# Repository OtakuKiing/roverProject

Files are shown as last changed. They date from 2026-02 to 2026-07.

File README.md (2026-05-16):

[//]: # (This is a comment format of Markdown files!)





# Project Overview

## What it is
Project Wayfinder is planned to be a relatively large (exact size TBD) autonomous rover vehicle, designed for 3D mapping and autonomous navigation via SLAM and computer vision algorithms. Designed from the ground up, the aim is to do much as possible via ground up implementation from first principles, while learning essential frameworks such as ROS2. 

The target design architecture: RasPi 4 (ROS2, autonomous nav and mapping), ESP32 (web interface and comms relay), Teensy 4.1 (microROS, real-time control)

## File Index

**[Arduino](/arduino)**  
    ├> [Local libraries](/arduino/lib)  
    ├> [Source Code](/arduino/src)  
    └> [Header files](/arduino/include)  

**[Ground Controller](/ground-controller)**  
		├> [ROS2](/ground-controller/ros2-workspace)
    └> [Python](/ground-controller/python) (via PyGame & PySerial)

**[Docs](/_docs)**  
    ├> [Assets](/_docs/assets)  
    ├> [Subversion Info](/_docs/versioning) (complete breakdowns of each subversion)  
    ├> [Electronics](/_docs/electronics)  
    └> [Hardware](/_docs/hardware)  

## Getting Started  
Check out [contributions](/CONTRIBUTING.md) before editing anything!

Wayfinder is built mainly on *Linux* infrastructure (specifically Ubuntu 22.04); alternatives will be mentioned where possible.  

- Clone this repo and install the PlatformIO extension in your IDE
- Follow the [ROS2 "Humble" install guide](https://docs.ros.org/en/humble/Installation/Ubuntu-Install-Debs.html)

## Status
**Focus**: Arduino + ROS2 fundamentals, test rig development  

 - [X] Set up dev environment (ROS2 Humble, PlatformIO, Git)
 - [X] Finalize parts list for first purchase
 - [X] Serial communication, PWM motor control, encoder reading
 - [ ] ROS2 practice: Publisher/subscriber nodes, serial communication
 - [X] Design V0 test rig in Onshape

## Team & Credits
Project Lead - Michael Yakubu  
Hardware Design - Faisal Ibrahim, Yahia Eltahir  
Software Engineering - TBD  
Electronics Design - TBD  

### License
See [LICENSE](/LICENSE) for more details.

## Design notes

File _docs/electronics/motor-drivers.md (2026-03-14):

# Motor Driver Boards

Driver boards which allow the motor to recieve commands from the real-time microcontroller. Though motors can theoretically be directly connected to the microcontroller, the 5V output and low current wouldn't be enough for anything beyond the smallest of hobby motors. There's also a risk of damaging the GPIO pins due to back EMF (motor sending high voltage back to power supply).

### In the specs...

Current is written as `[max continuous draw]/[peak draw]`.  
Safety margin is calculated as `[max continouos draw]/[peak motor draw]`.

## V0
### Options and Specs
**Model A**: [Dual channel 10A](https://thepihut.com/products/10a-5v-30v-2-channel-dc-motor-driver)  
**Specs**:  
 - Channels: 2  
 - Current: 10/30A  
 - Voltage: 5/30V  
 - Reverse Polarity Protection (RPP): No  
 - I/O Pins: 4  
 - Cost: £22.20  

**Model B**: [Dual channel 7A](https://thepihut.com/products/2x7a-dc-motor-driver)  
**Specs**:  
 - Channels: 2  
 - Current: 7/50A  
 - Voltage: 7/24V  
 - Reverse Polarity Protection (RPP): Yes  
 - I/O Pins: 6  
 - Cost: £20.20  

**Model C**: [Single channel 43A](https://www.amazon.co.uk/JZK-BTS7960B-Double-Stepper-H-Bridge/dp/B09HGBM5D2)  
**Specs**:  
 - Channels: 1  
 - Current: 43A (likely cont.)  
 - Voltage: 5.5/27V  
 - Reverse Polarity Protection (RPP): N/A  
 - I/O Pins: 6 
 - Cost: £7.19  

### Key Notes and Comparisons
- Model C is a single channel board and thus is the cheapest option; one board per motor means greater redundancy, but takes up more space.  
- Model C also seems to have the highest continuous current output per channel (unconfirmed), more than 6x that of Model B. However, the V0 motors draw a max of 7A each, so only Model A lacks a safety margin.  
- Model A lacks RPP, but this can be mitigated via thorough wiring checks.  

### Final Decision
**Model A** is the best V0 choice - it has the most appropriate safety margin, and requires the fewest I/O pins for full control. The lack of RPP does pose risk, but this is offset by its clear labelling and addition of test buttons. Model B can also easily be used as an alternative, though not at full motor load.

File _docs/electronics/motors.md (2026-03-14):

# Motors

High quality motors are an essential component for any mobile vehicle project, and so selecting the appropriate models is key.
  
## In the specs...
Encoder values are written as `[motor shaft count]/[output shaft count]` CPR (Counts Per Revolution). For example, a `24/72` CPR encoder reads at 24 CPR on the motor shaft and 72 CPR on the output shaft, describing a 1:3 geared motor.  
Current values are written as `[min. current]/[stall current]` A. For example, a `0.35/6` A motor runs at 0.35A under no load ad has a maximum draw of 6A.

## V0
### Options and Specs
**Model A**: [12V 251RPM 18kgcm](https://thepihut.com/products/metal-dc-geared-motor-w-encoder-12v-251rpm-18kg-cm)  
**Specs**:  
 - Output Shaft: 6mm D-shaft
 - Torque: 18kgcm  
 - Speed: 251 RPM  
 - Encoder: 16/700 CPR, Hall sensor
 - Voltage: 12V  
 - Current: 0.35/7A  
 - Weight: 205g
 - Cost: £15.90  

**Model B**: [12V 122RPM 38kgcm](https://thepihut.com/products/metal-dc-geared-motor-w-encoder-12v-122rpm-38kg-cm)  
**Specs**:  
 - Output Shaft: 6mm D-shaft
 - Torque: 38kgcm  
 - Speed: 122 RPM  
 - Encoder: 16/1440 CPR, Hall sensor
 - Voltage: 12V  
 - Current: 0.35/7A  
 - Weight: 205g
 - Cots: £27.90    

### Key Notes & Comparisons
Model B has more than 2x more torque than Model A, but this is unimportant as both can handle the full weight of V0.  
Using 80mm wheels at half of max RPM, Model A and B could achieve `pi*0.08*125.5/60 = 0.53 m/s` and `pi*0.08*61/60 = 0.26 m/s` respectively due to RPM differences.  
B has double the effective encoder precision, but this is unimportant as precise wheel precision is unnecessary here.
B is also twice as expensive due to the higher internal gear ratio.

### Final Decision
**Model A** is the best V0 choice - much lower cost while providing a suitably modest amount of torque and encoder accuracy compared to alternatives. It has (at best) double the velocity and still matches power system requirements perfectly. The 6mm D-shaft is also a common size and suits many COTS wheels via direct drive.

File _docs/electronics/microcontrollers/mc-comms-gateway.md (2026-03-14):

# Communication Gateway
Wireless communication is a must for any autonomous vehicle, allowing live data streams to be viewed and remote control overrides. This task could be given to a dedicated microcontroller for better micromanagement, or added onto an existing MCU for lower latency/complexity and fewer failure points.  

### In the specs...
Describe how specs are laid out + other info that may help understand the page

## V0
### Options and Specs  
**Model A**: [ESP32-S3](Link)  
**Specs**:  
 - Supported protocols: 
 - Wireless transfer rate:  
 - Max range:  
 - Frequency:  
 - GPIO: 13
 - Cost:

**Model B**: [Item](Link)  
**Specs**:  
 - Supported protocols:
 - Wireless transfer rate:  
 - Max range:  
 - Frequency:  
 - GPIO:
 - Cost:

### Key Notes & Comparisons

### Final Decision

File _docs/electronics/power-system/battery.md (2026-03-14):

# Battery  
Short description describing component and its importance  

### In the specs...  
Discharge rate is written as `[Max continuous current]/[Peak current]`.  

## V0  
### Options and Specs
**Model A**: [3S 2200mAh LiPo battery](https://overlander.co.uk/product/2200mah-11-1v-3s-35c-supersport-pro-lipo-battery/)  
**Specs**:  
 - Capacity: 2200mAh
 - Discharge rate: 77/143A
 - Voltage: 11.1V
 - Weight: 169g
 - Cost: £17.99

**Model B**: []()  
**Specs**:  
 - Capacity: 
 - Discharge rate: 
 - Voltage: 
 - Weight: 
 - Cost:

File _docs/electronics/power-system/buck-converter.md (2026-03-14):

# Buck Converter
Different components often operate at different voltages, but a battery can only provide one voltage level. You could use several batteries to group a system into its various voltages, but a much simpler solution is to convert, for example, 12V into 5V using a buck converter.

### In the specs...
Describe how specs are laid out + other info that may help understand the page

## V0
### Options and Specs  
**Model A**: [5V 1.2A MPM3610](https://thepihut.com/products/adafruit-mpm3610-5v-buck-converter-breakout-21v-in-5v-out-at-1-2a)  
**Specs**:  
 - V-in: 6/21V
 - V-out: 5V
 - Max current: 1.2A
 - Pre-soldered: No
 - Cost: £6.00

**Model B**: [20W Adjustable Converter](https://thepihut.com/products/20w-adjustable-dc-dc-buck-converter-with-digital-display)  
**Specs**:  
 - V-in: 4/40V
 - V-out: 3V3/5V
 - Max current: 5/3A
 - Pre-soldered: Yes
 - Cost: £4.70 

### Key Notes & Comparisons
Model A only outputs a fixed voltage and current, whereas B can provide a wide range (6W vs 20W respectively).
A is potentially much cooler than B at the same voltage due to its lower max current.
A has a significantly smaller footprint than B, but lacks conveniences such as self-calibration and RPP.

### Final Decision
**Model B** is the best choice for V0, as it has a much larger safety margin in terms of current, can output over twice as much power, and comes with pre-soldered connectors. The adjustable voltage also means it can be re-used for other components. Model A may be good for future use in isolated circuits where space and simplicity are essential.

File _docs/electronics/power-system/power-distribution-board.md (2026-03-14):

# Power Distribution Board
Short description describing component and its importance
  
### In the specs...
Describe how specs are laid out + other info that may help understand the page

## V0
### Options and Specs  
**Model A**: [Item](Link)  
**Specs**:  
 - Max V-out:
 - Max current:
 - Channels:
 - Connectors:
 - Cost:

**Model B**: [Item](Link)  
**Specs**:  
 - Max V-out:
 - Max current:
 - Channels:
 - Connectors:
 - Cost:   

### Key Notes & Comparisons

### Final Decision

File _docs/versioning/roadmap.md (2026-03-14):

# Roadmap
> A quick index of each version, including subversions.

| Version | Name | Status | Summary |
|---|---|---|---|
| v0.0 | Keyframe | Active | 2WD test rig, closed-loop PID |
| v0.1 | Crawler | Planned | ROS2 nodes, PlotJuggler |
| v1.0 | TBD | Planned | 4WD platform, sonar |
| v2.0 | TBD | Planned | RasPi, first SLAM attempt |
| vF | Wayfinder | Target | Full LiDAR/vision UGV |

## Progression Summary

```text
V0:
    Hardware:	      2WD, Differential steering, 3DP/Lasercut chassis
    Sensors:	      Wheel encoders, Buzzer, IMU
    Controllers:	  Arduino (C++)

V1:
    Hardware:	      4WD, Differential steering, COTS/Lasercut chassis
    Sensors:	      Wheel encoders, Buzzer, Sonar, LED screen
    Controllers:	  Arduino (C++), ESP32-S3

V2:
    Hardware:	      4WD, Differential steering, Aluminum chassis
    Sensors:	      Wheel encoders, Buzzer, Sonar, LED screen, Environmental sensor suite
    Controllers:	  Arduino (C++), ESP32-S3, RasPi 4B

...	etc

VF:
    Application:    Area mapping, surveillance, data collection, payload delivery, endurance missions,
    Hardware:       Aluminum chassis, AWD, AWS(?), Independent suspension 
    Sensors:        Odometry, LoRa telemetry, RTK GPS, LiDAR SLAM, Vision, Speakers, Lights
    Controllers:    Teensy 4.1 <-> ESP32 <-> RasPi, (micro)ROS2
    Modules:        [Stretch goals!] Robotic arm, Drone launcher, Solar 
```

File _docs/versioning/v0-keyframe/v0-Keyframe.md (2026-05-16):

# v0 "Keyframe"

> First stable closed-loop control on the 2WD test rig.

## Hardware
- **Chassis:** Lasercut wood plates
- **Motion:** 2WD differential
- **Controllers:** Arduino UNO R3
- **Sensors:** Wheel encoders, IMU (MPU6050)

## Firmware
- PID velocity controller
- Pygame serial bridge node
- Basic telemetry publisher

## Changelog

<details>
<summary><h2 style="display:inline">v0.0 "VERSION"</h2></summary>

### Added
- New stuff

### Fixed
- N/A

### Known Issues / Limitations
- Stuff that needs to be fixed

### Up Next
- What this lets us do next

</details><br>

<details>
<summary><h2 style="display:inline">v0.1 "Keyframe"</h2></summary>

### Added
- New stuff

### Fixed
- Fixed stuff

### Known Issues / Limitations
- Stuff that needs to be fixed

### Up Next
- What this lets us do next

</details>

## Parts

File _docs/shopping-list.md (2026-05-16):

# Shopping List

Parts listed in order of importance. `---` notates sets that should be **bought together** for each subversion.
Most parts come from the Pi Hut, but some may be sourced from sites such as Pimoroni or elsewhere.

| Component | Quantity | Cost £ |
| --- | --- | --- |
| **V0** | | |
| ~~[Arduino UNO R3](https://thepihut.com/products/arduino-uno-rev-3)~~																				 | 1 | 24.50  |
| ~~[12V motor w/ encoder](https://thepihut.com/products/metal-dc-geared-motor-w-encoder-12v-251rpm-18kg-cm)~~ | 2 | 31.80  |
| ~~[Half-size breadboard](https://thepihut.com/products/raspberry-pi-breadboard-half-size)~~									 | 1 | 3.00 |
| ~~[DuPont Wires](https://thepihut.com/products/thepihuts-jumper-bumper-pack-120pcs-dupont-wire)~~ | 1 | 6.00 |
| ~~[Piezo Buzzer](https://thepihut.com/products/piezo-buzzer)~~ | 1 | 1.30 |
| ~~[Electrolytic Capacitors](https://thepihut.com/products/200-piece-ultimate-capacitor-kit)~~ | 1 | 6.00 |
| ~~[Motor driver board](https://thepihut.com/products/10a-5v-30v-2-channel-dc-motor-driver)~~ | 1 | 22.20  |
| ~~[DC Jack to Screw Terminal]()~~ | 1 | 5.99 |
| ------------------------------------------- | -------- | 100.70 |
| ------------------------------------------- | -------- | ------ |
| [IMU](https://thepihut.com/products/adafruit-mpu-6050-6-dof-accel-and-gyro-sensor-stemma-qt-qwiic) | 1 | 8.00 |
| [Voltage/Current Sensor](https://thepihut.com/products/adafruit-ina260-high-or-low-side-voltage-current-power-sensor-ada4226)  | 1 | 9.60  | | -------- | ------ |
| [Buck converter](https://thepihut.com/products/dc-dc-buck-mini-module-3-3v-5v) | 2 | 6.80 |
| [Raspberry Pi Heatsink w/ Fan](https://thepihut.com/products/dual-fan-heatsink-case-for-raspberry-pi-4) | 1 | 14.00  |
| [Hubs](https://thepihut.com/products/pololu-universal-aluminium-mounting-hub-for-6mm-shafts-m3-holes-2-pack) | 1 | 12.50  |
| [80mm Wheels](https://thepihut.com/products/pololu-wheel-80x10mm-pair-black) | 1 | 8.40 |
| [3S 2200mAh LiPo battery](https://overlander.co.uk/product/2200mah-11-1v-3s-35c-supersport-pro-lipo-battery/)| 1 | 17.99  |
| [LiPo charger](https://overlander.co.uk/product/overlander-rc-3s-lipo-charger/) | 1 | 16.99  |
| [LiPo safety charge sack](https://overlander.co.uk/product/lipo-safety-charge-sack) | 1 | 7.99 |
| Shipping | -------- | 7.50 |
| **Subtotal** | -------- | 109.77 |
| | | |
| **V1** | | |
| [ESP32-S3](https://thepihut.com/products/adafruit-esp32-s3-feather-with-4mb-flash-2mb-psram-stemma-qt-qwiic) | 1 | 16.80  |
| [Teensy 4.1](https://thepihut.com/products/teensy-4-1-with-assembled-pins) | 1 | 34.60  |
| Aluminum extrusion | xxx | xxx |
| ------------------------------------------- | -------- | ------ |
| [BNO055 IMU](https://thepihut.com/products/adafruit-9-dof-absolute-orientation-imu-fusion-breakout-bno055) | 1 | 33.60  |
| [NEO-6M GPS](https://thepihut.com/products/adafruit-ultimate-gps-breakout-66-channel-w-10-hz-updates) | 1 | 28.80  |
| **Subtotal** | -------- | 113.80 |
| | | |
| **V2** | | |
| [RasPi 4B](https://thepihut.com/products/raspberry-pi-4-model-b) | 1 | 81.60  |
| [Ethernet for Teensy 4.1](https://thepihut.com/products/ethernet-kit-for-teensy-4-1) | 1 | 9.60 |
| ------------------------------------------- | -------- | ------ |
| [RPLIDAR](https://www.mouser.co.uk/ProductDetail/DFRobot/DFR0315?qs=kE1vTINknaX%252Bruj42CnW2Q%3D%3D) | 1 | 89.20  |
| [C270 camera](https://www.argos.co.uk/product/4034924) | 1 | 17.99  |
| **Subtotal** | -------- | 198.39 |
| | | |
| **Total** | | 493.26 |

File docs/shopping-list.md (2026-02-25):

# Shopping List

Parts listed in order of importance. `---` notates sets that should be **bought together** for each subversion.
Most parts come from the Pi Hut, but some may be sourced from sites such as Pimoroni or elsewhere.

| Component | Quantity | Cost £ |
| --- | --- | --- |
| **V0** | | |
| [Arduino UNO R3](https://thepihut.com/products/arduino-uno-rev-3)																						 | 1 | 24.50  |
| [12V motor w/ encoder](https://thepihut.com/products/metal-dc-geared-motor-w-encoder-12v-251rpm-18kg-cm) | 2 | 31.80  |
| [Half-size breadboard](https://thepihut.com/products/raspberry-pi-breadboard-half-size)											 | 1 | 3.00 |
| [DuPont Wires](https://thepihut.com/products/thepihuts-jumper-bumper-pack-120pcs-dupont-wire) 		 | 1 | 6.00 |
| [Piezo Buzzer](https://thepihut.com/products/piezo-buzzer) | 1 | 1.30 |
| [Electrolytic Capacitors](https://thepihut.com/products/200-piece-ultimate-capacitor-kit) | 1 | 6.00 |
| [Motor driver board](https://thepihut.com/products/10a-5v-30v-2-channel-dc-motor-driver) | 1 | 22.20  |
| [DuPont Wires](https://thepihut.com/products/thepihuts-jumper-bumper-pack-120pcs-dupont-wire) | 1 | 6.00 |
| [IMU](https://thepihut.com/products/adafruit-mpu-6050-6-dof-accel-and-gyro-sensor-stemma-qt-qwiic) | 1 | 8.00 |
| ------------------------------------------- | -------- | ------ |
| Assembly hardware | 1 | 30.00  |
| 6mm Birch Plywood | 1 | 20.00  |
| [Hubs](https://thepihut.com/products/pololu-universal-aluminium-mounting-hub-for-6mm-shafts-m3-holes-2-pack) | 1 | 12.50  |
| [Wheels](https://thepihut.com/products/pololu-wheel-80x10mm-pair-black) | 1 | 8.40 |
| [Caster wheels](https://thepihut.com/products/20mm-height-metal-caster-bearing-wheel) | 1 | 1.90 |
| ------------------------------------------- | -------- | ------ |
| [3S 2200mAh LiPo battery](https://overlander.co.uk/product/2200mah-11-1v-3s-35c-supersport-pro-lipo-battery/)| 1 | 17.99  |
| [LiPo charger](https://overlander.co.uk/product/overlander-rc-3s-lipo-charger/) | 1 | 16.99  |
| [LiPo safety charge sack](https://overlander.co.uk/product/lipo-safety-charge-sack) | 1 | 7.99 |
| [LiPo Voltage Alarm](https://www.hobbyrc.co.uk/1-8s-cell-checker-with-low-voltage-alarm) | 1 | 2.60 |
| [Buck converter](ttps://thepihut.com/products/20w-adjustable-dc-dc-buck-converter-with-digital-display) | 2 | 4.70 |
| **Subtotal** | -------- | 191.07 |
| | | |
| **V1** | | |
| [ESP32-S3](https://thepihut.com/products/adafruit-esp32-s3-feather-with-4mb-flash-2mb-psram-stemma-qt-qwiic) | 1 | 16.80  |
| [Teensy 4.1](https://thepihut.com/products/teensy-4-1-with-assembled-pins) | 1 | 34.60  |
| Aluminum extrusion | xxx | xxx |
| ------------------------------------------- | -------- | ------ |
| [BNO055 IMU](https://thepihut.com/products/adafruit-9-dof-absolute-orientation-imu-fusion-breakout-bno055) | 1 | 33.60  |
| [NEO-6M GPS](https://thepihut.com/products/adafruit-ultimate-gps-breakout-66-channel-w-10-hz-updates) | 1 | 28.80  |
| **Subtotal** | -------- | 113.80 |
| | | |
| **V2** | | |
| [RasPi 4B](https://thepihut.com/products/raspberry-pi-4-model-b) | 1 | 81.60  |
| [Ethernet for Teensy 4.1](https://thepihut.com/products/ethernet-kit-for-teensy-4-1) | 1 | 9.60 |
| ------------------------------------------- | -------- | ------ |
| [RPLIDAR](https://www.mouser.co.uk/ProductDetail/DFRobot/DFR0315?qs=kE1vTINknaX%252Bruj42CnW2Q%3D%3D) | 1 | 89.20  |
| [C270 camera](https://www.argos.co.uk/product/4034924) | 1 | 17.99  |
| **Subtotal** | -------- | 198.39 |
| | | |
| **Total** | | 493.26 |

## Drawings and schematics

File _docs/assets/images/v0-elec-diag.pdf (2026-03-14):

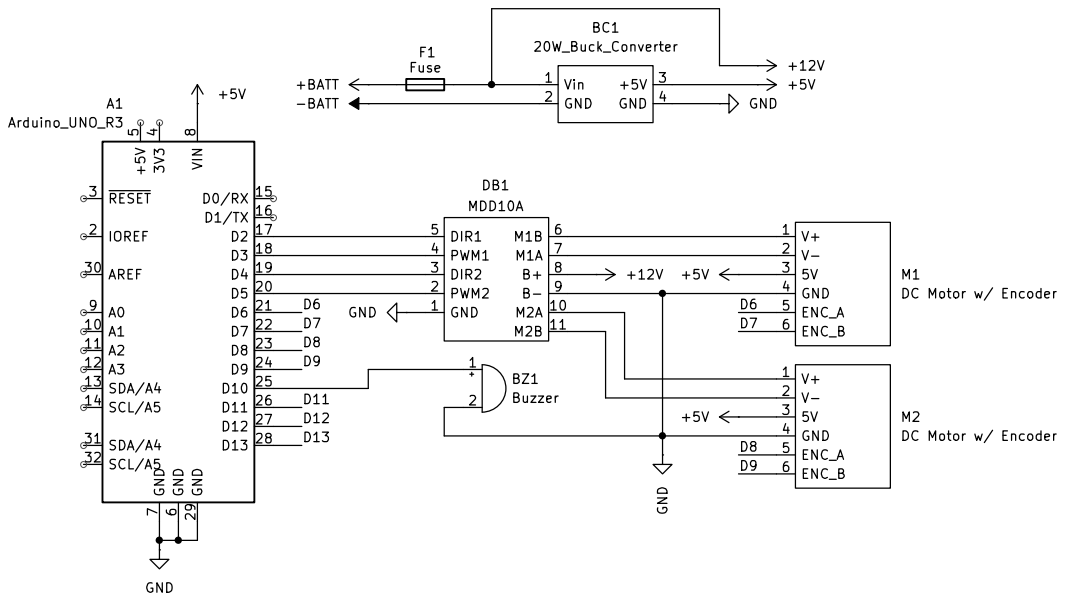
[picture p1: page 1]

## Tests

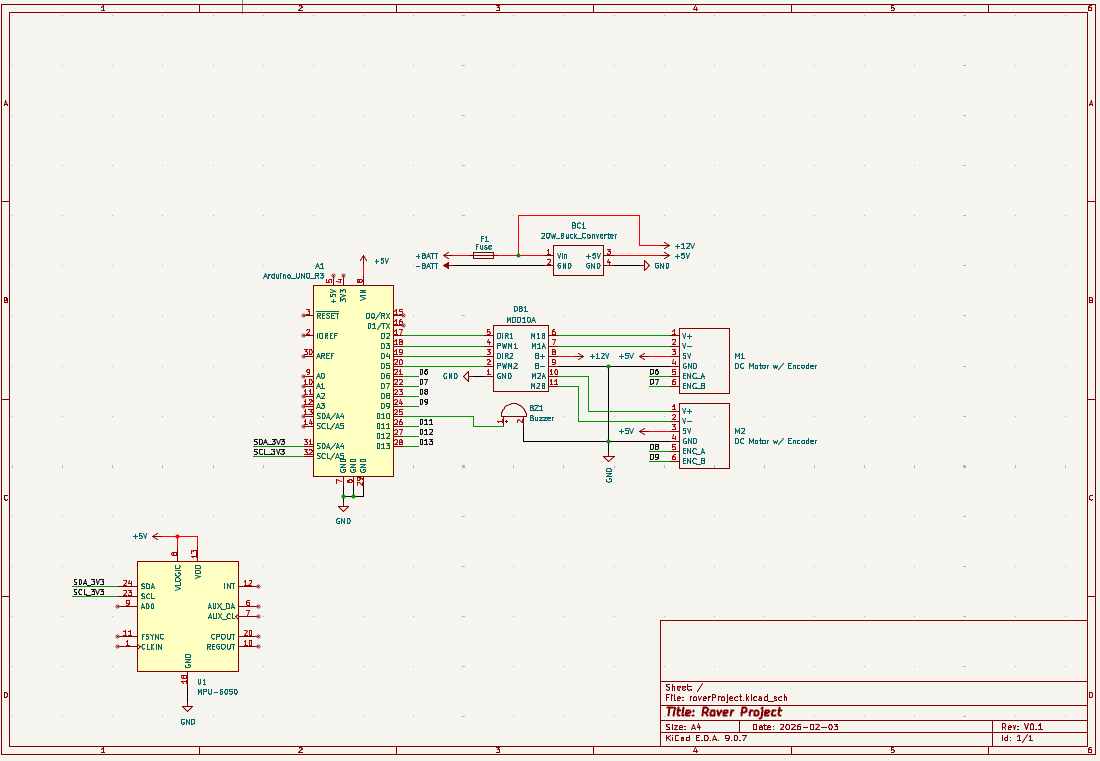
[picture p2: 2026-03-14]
_docs/assets/images/v0-img-test.PNG

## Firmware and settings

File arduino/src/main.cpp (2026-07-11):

#include "pch.h"

float motor0_Target_RPM;
float motor1_Target_RPM;
float dummy_Data = 37.0f;  // debug line
Packet p0 = {};
Packet p1 = {};
Packet p2 = {};

void serialControlInput() {
  serialRead();

	switch (target_Id) {
		case 0x00:
			motorsKill();
			break;

		case 0x01:
			motor0_Target_RPM = (float)target_Speed * 251.0f / 255.0f;
			motor0Move(target_Dir, target_Speed);
			break;

		case 0x02:
			motor1_Target_RPM = (float)target_Speed * 251.0f / 255.0f;
			motor1Move(target_Dir, target_Speed);
			break;
	}
}

void serialControlOutput() {
	p0.id = {0x01};  // test, unsigned data
	memcpy(&p0.byte1, &motor0_RPM, sizeof(float));
	serialWrite(p0);

	p1.id = {0x02};  // test, unsigned data
	memcpy(&p1.byte1, &motor1_RPM, sizeof(float));
	serialWrite(p1);

	p2.id = {0x81};  // test, unsigned data
	memcpy(&p2.byte1, &imu_Accel.x, sizeof(float));
	serialWrite(p2);
}

void setup() {
  motorsInit();
  encodersInit();
  serialInit();
	imuInit();
  pinMode(LED_PIN, OUTPUT);  // onboard LED has no pwm
}

void loop() {
	imuGetData();
	//shake(1);
	motorsSpeedDistance();	// update all motor values

	serialControlInput();  // read serial
	serialControlOutput();  // write to serial
}

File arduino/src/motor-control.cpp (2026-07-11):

#include "Arduino.h"

/* TODO:
 - Double check the MOTOR_CPR value - 16 or 64?
 - Add simple autonomous functions ie 'forward(distance, speed)' to a separate file
 - Test best value for CALC_RATE_MS
*/

// --- Declarations --- //

// pins to motor driver board (JZK BTS7960B)
const int MOTOR_0_L_PWM = 5; 
const int MOTOR_0_R_PWM = 6; 
const int MOTOR_1_R_PWM = 9; 
const int MOTOR_1_L_PWM = 10; 

// pins to motor encoders
// encoder counts are more significantly reliable when pins are interrupt capable
// UNO R3 only has interrupt pins 2 and 3
const int MOTOR_0_ENCA = 2;  // interrupt
const int MOTOR_0_ENCB = 4; 
const int MOTOR_1_ENCA = 3;  // interrupt
const int MOTOR_1_ENCB = 7; 

// store previous encoder channel for comparison
byte motor0_EncA_Last;
byte motor0_EncB_Last;
byte motor1_EncA_Last;
byte motor1_EncB_Last;

// rpm & distance travelled calculation values
const int CALC_RATE_MS = 100;  // rate at which speeds and distance are calculated in ms
const int MOTOR_CPR = 1400;	// encoder attached to output shaft
const float WHEEL_DIAM = 0.08;  // diameter in metres
const float WHEEL_CIRC = PI * WHEEL_DIAM; // circumference in metres

float motor0_RPM = 0.0;  // speed in revolutions per minute
float motor1_RPM = 0.0;
float motor0_MPS = 0.0;  // speed in metres per second
float motor1_MPS = 0.0;
float motor0_Distance = 0.0;  // cumulative distance travelled
float motor1_Distance = 0.0;

volatile int motor0_Duration;  // the number of the pulses counted
volatile int motor1_Duration;

volatile bool motor0_Direction;  // the rotation direction
volatile bool motor1_Direction;  

uint32_t motors_Before;  // last time motor rpm was checked

// --- Functions --- //

void encoder0Raw() {  // convert encoders signals to counts and direction
    int encA_State = digitalRead(MOTOR_0_ENCA);  // current 'A' value
    int encB_State = digitalRead(MOTOR_0_ENCB);  // current 'B' value

		if(motor0_EncB_Last == encB_State) {  // if 'B' is the same...
				motor0_Direction = (encA_State == HIGH) ? true : false;  // ...then only 'A' must have changed, so direction based off of 'A'...
		} else {
				motor0_Direction = (encB_State == encA_State) ? true : false;  // else direction based off of 'B' relative to 'A'
		}
		(!motor0_Direction) ? ++motor0_Duration : --motor0_Duration; // incrementing pulse counter

    motor0_EncA_Last = encA_State;
    motor0_EncB_Last = encB_State; 
}

void encoder1Raw() {  // convert encoders signals to counts and direction
    int encA_State = digitalRead(MOTOR_1_ENCA);  // current 'A' value
    int encB_State = digitalRead(MOTOR_1_ENCB);  // current 'B' value

    
		if(motor1_EncB_Last == encB_State) {  // if 'B' is the same...
				motor1_Direction = (encA_State == HIGH) ? true : false;  // ...then only 'A' must have changed, so direction based off of 'A'...
		} else {
				motor1_Direction = (encB_State == encA_State) ? true : false;  // else direction based off of 'B' relative to 'A'
		}
		(!motor1_Direction) ? ++motor1_Duration : --motor1_Duration; // incrementing pulse counter


    motor1_EncA_Last = encA_State;
    motor1_EncB_Last = encB_State;
}

void motorsInit() {  // initialize motor pins
	pinMode(MOTOR_0_L_PWM, OUTPUT);
	pinMode(MOTOR_0_R_PWM, OUTPUT);
	pinMode(MOTOR_1_L_PWM, OUTPUT);
	pinMode(MOTOR_1_R_PWM, OUTPUT);
	analogWrite(MOTOR_0_L_PWM, 0); 
	analogWrite(MOTOR_0_R_PWM, 0); 
	analogWrite(MOTOR_1_L_PWM, 0); 
	analogWrite(MOTOR_1_R_PWM, 0); 

	motors_Before = millis();
}

void encodersInit() {  // initialize encoder pins
	pinMode(MOTOR_0_ENCA, INPUT_PULLUP);
	pinMode(MOTOR_1_ENCA, INPUT_PULLUP);
	pinMode(MOTOR_0_ENCB, INPUT_PULLUP);
	attachInterrupt(digitalPinToInterrupt(MOTOR_0_ENCA), encoder0Raw, CHANGE);
	pinMode(MOTOR_1_ENCB, INPUT_PULLUP);
	attachInterrupt(digitalPinToInterrupt(MOTOR_1_ENCA), encoder1Raw, CHANGE);

	motor0_EncA_Last = digitalRead(MOTOR_0_ENCA);
	motor0_EncB_Last = digitalRead(MOTOR_0_ENCB);
	motor1_EncA_Last = digitalRead(MOTOR_1_ENCA);
	motor1_EncB_Last = digitalRead(MOTOR_1_ENCB);
}

void motorsSpeedDistance() {  // get raw motor values and convert to rpm/mps

	uint32_t motors_Now = millis();
	uint32_t motors_dt = motors_Now - motors_Before;
	
	if(motors_dt >= CALC_RATE_MS) {  // Calculate every >100ms
		noInterrupts();  // stop duration from being changed during calculations
		long dur0 = motor0_Duration;
		long dur1 = motor1_Duration;
		motor0_Duration = 0;
		motor1_Duration = 0;
		interrupts();

		// rpm = (counts / (counts per revolution)) / (time in minutes)
		motor0_RPM = (float(dur0) / MOTOR_CPR) / (motors_dt / 60000.0f);
		motor1_RPM = (float(dur1) / MOTOR_CPR) / (motors_dt / 60000.0f);
		
		motor0_MPS = motor0_RPM * WHEEL_CIRC / 60.0f;
		motor1_MPS = motor1_RPM * WHEEL_CIRC / 60.0f;

		motor0_Distance += motor0_MPS * (motors_dt / 1000.0f);
		motor1_Distance += motor1_MPS * (motors_dt / 1000.0f);

		motors_Before = motors_Now;
	}
}

void motor0Move(bool direction, int speed) {  // simple direction and speed controls
	// kill PWM first 
	analogWrite(MOTOR_0_L_PWM, 0); 
	analogWrite(MOTOR_0_R_PWM, 0); 

	speed = speed * 0.6;  // m1 is broken? half speed to match limits
	if (direction==0) {analogWrite(MOTOR_0_L_PWM, speed);} 
	else {analogWrite(MOTOR_0_R_PWM, speed);}
}

void motor1Move(bool direction, int speed) {  // simple direction and speed controls
	// kill PWM first 
	analogWrite(MOTOR_1_L_PWM, 0); 
	analogWrite(MOTOR_1_R_PWM, 0); 

	//speed = speed / 2;
	if (direction==0) {analogWrite(MOTOR_1_L_PWM, speed);} 
	else {analogWrite(MOTOR_1_R_PWM, speed);}
}

bool motorsKill() {  // completely cuts power to motors
	// set all pins to LOW output
	digitalWrite(MOTOR_0_R_PWM, LOW);
  digitalWrite(MOTOR_1_R_PWM, LOW);
  digitalWrite(MOTOR_0_L_PWM, LOW);
  digitalWrite(MOTOR_1_L_PWM, LOW);
	return(true);
}

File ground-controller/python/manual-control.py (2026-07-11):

# TODO: 
# split into nicer functions - better grouping!
# test controller inputs

'''
| Direction     | Category  | Message ID | Content                                           |
| ------------- | --------- | ---------- | ------------------------------------------------- |
| Pi -> Arduino | Admin     | 0x00       | Emergency state X - run routine and await command |
|               |           | 0x01       | Exit emergency state                              |
|               |           | 0x02       | Toggle verbose telemetry                          |
|               |           | 0x03       | Toggle audio alerts                               |
|               |           | 0x04       | Debug 1 (eg live PID)                             |
|               |           | 0x05       | Debug 2 (eg live PID)                             |
|               | Command   | 0x10       | Move motors                                       |
|---------------|-----------|------------|---------------------------------------------------|
| Arduino -> Pi | Admin     | 0x80       | Error (eg missing expected component)             |
|               | Telemetry | 0x90       | Motors RPM                                        |
|               |           | 0x91       | Motors voltage                                    |
|               |           | 0x92       | Motors current                                    |
|               |           | 0x93       | Encoder counts (verbose)                          |
|               |           | 0xA0       | Battery voltage and current                       |
|               |           | 0xA1       | Battery temperature                               |
|               |           | 0xB0       | Raw IMU                                           |
|               |           | 0xB1       | Raw GNSS                                          |
|---------------|-----------|------------|---------------------------------------------------|
| Bidirectional | Admin     | 0xFE       | Heartbeat                                         |
'''

# Example file
import pygame, serial, time, queue, struct, threading
import serial.tools.list_ports

# pygame setup
pygame.init()
running = True

pygame.joystick.init()
joysticks = []

screen = pygame.display.set_mode((640, 400))
screen.fill((15, 15, 15))  # RGB fill
pygame.display.flip()  # update screen
pygame.display.set_caption("Input Window")

font = pygame.font.Font('freesansbold.ttf', 32)

text1 = font.render('W = Forwards, S = Backwards', True, (0,255,0), (0,0,255))
textRect1 = text1.get_rect()
textRect1.center = (320, 100)

text2 = font.render('A = Sweep Left, D = Sweep Right', True, (0,255,0), (0,0,255))
textRect2 = text2.get_rect()
textRect2.center = (320, 68)

text3 = font.render('Q = Pivot Left, E = Pivot Right', True, (0,255,0), (0,0,255))
textRect3 = text3.get_rect()
textRect3.center = (320, 36)

hud = pygame.Surface((640, 400), pygame.SRCALPHA)
hud.blit(text1, textRect1)
hud.blit(text2, textRect2)
hud.blit(text3, textRect3)


### serial setup ###

serial_thread = None
serial_Queue = queue.Queue()
prev_Packet_Out = None
header = 0
heartbeat1 = 0
awaiting_ACK = False

raw_Ser: serial.Serial | None = None

while raw_Ser == None:  # search for arduino
  all_Ports = serial.tools.list_ports.comports()	# get all open serial ports
  for comport in all_Ports:
    if "arduino" in comport.description.lower():
      raw_Ser = serial.Serial(port=comport.device, baudrate=115200, timeout=1)  # open serial port @ 115200 baud
      print(f"Serial port: {raw_Ser.name or "unknown"}\nBaud: {raw_Ser.baudrate}")  # print which port and baud was really used
      break

  if raw_Ser == None: print("No port available")

## motor data input ##
prev_Speed_L = 0
prev_Dir_L = 0
prev_Speed_R = 0
prev_Dir_R = 0

motor0_RPM = 0.0
motor1_RPM = 0.0

imu = 0.0

def serialSendUrgent(packet_Out):  # drain the queue
    while not serial_Queue.empty():
        try: serial_Queue.get_nowait()
        except queue.Empty: break
    serial_Queue.put(packet_Out)

def serialIO():
  global running, motor0_RPM, motor1_RPM, heartbeat1, awaiting_ACK  # allows these variables to be modified globally
  header = 0
  packet_Out = b''
  while running:
    time.sleep(0.001)
    ### serial control	###
    assert raw_Ser is not None

    ## heartbeat ##
    now = time.perf_counter()  # time now in ms
    if now - heartbeat1 > 0.5:  # send heartbeat after 0.5s with no command sent
      raw_Ser.write(b'\xFF\xFE')
      heartbeat1 = time.perf_counter()
      awaiting_ACK = True

    ## write serial ##
    try:
      packet_Out = serial_Queue.get_nowait()
      if packet_Out is not None:
        raw_Ser.write(packet_Out)
        print("Sent this:", packet_Out)
        heartbeat1 = time.perf_counter()
      else: break   # sentinel command, exit
    except queue.Empty:
      pass

    ## read serial ##
    if raw_Ser.in_waiting:
      byte = raw_Ser.read(1)
    else: byte = b''
      
    if byte == b'\xFF' and header == 0:  # resets loop, don't send header to match-case
      header = 1  
      continue

    if header == 1:  # match packet structure to command database
      match byte:
        case b'\x01':  # motor0 data
          header = 0
          packet_In = raw_Ser.read(4)
          if len(packet_In) == 4:  # check if packet is valid
            motor0_RPM = struct.unpack('<f', packet_In)[0]  # convert bytes from array to little-endian float
            # print("Recieved from motor0:", motor0_RPM) # debug line
          else:
            print("Bad packet! motor0")

        case b'\x02':  # motor1 data
          header = 0
          packet_In = raw_Ser.read(4)
          if len(packet_In) == 4:  # check if packet is valid
            motor1_RPM = struct.unpack('<f', packet_In)[0]  # convert bytes from array to little-endian float
            # print("Recieved from motor1:", motor1_RPM) # debug line
          else: 
            print("Bad packet! motor1")
            
        case b'\x81':  # motor1 data
          header = 0
          packet_In = raw_Ser.read(4)
          if len(packet_In) == 4:  # check if packet is valid
            imu = struct.unpack('<f', packet_In)[0]  # convert bytes from array to little-endian float
            print("Recieved from imu:", imu) # debug line
          else: 
            print("Bad packet! motor1")
        
        case b'\xFE':  # heartbeat ACK
          awaiting_ACK = False
          header = 0

        case b'\x00':  # e-stop active
          print("E-stop active!")
          header = 0

        case _:  # ignore bad data
          header = 0
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

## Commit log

2026-02-25 Update manual-control.py & serial-control.cpp
    Amend main.cpp to make LED respond to error codes only
    Update serial-control.cpp to add a heartbeat timer
    Amend manual-control.py to standardise indentation and add heartbeat timer
    [main.cpp, manual-control.py, serial-control.cpp]
2026-03-08 Update manual-control.py
    Update manual-control.py to add serial communication to a separate thread
    Amend main.cpp to separate code into functions
    Amend serial-control.cpp to simplify code and make variables more readable
    Amend motor-control.cpp to standardize indentation, remove redundant checks, and correctly assign float values
    [main.cpp, manual-control.py, motor-control.cpp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]
2026-03-14 Repo Refactoring
    General tidying of the docs and putting files where they need to be.
    No code edited, only moved.
    [roverProject.kicad_sch]
2026-05-16 Fix serial communication
    Changed all hexadecimal references to motor0 and motor1 to 0x01 and 0x02 respectively
    Fixed error where main.cpp only sent 1 of 4 data bytes
    Fixed error where serial-control.cpp ignored changes to target_Speed
    Fixed error where ground-controller.py interpreted float inputs as integer
    [main.cpp, manual-control.py, motor-control.cpp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]
2026-05-16 Amend main.cpp
    Set motorX_Target_RPM to be a float instead of an int, which uses 4 bytes over 1
    Fixed issue in main.cpp where only 1 of 4 motor telemetry bytes was copied to serial
    Added message ID table
    [main.cpp, manual-control.py, serial-control.cpp]
2026-06-04 Add HUD to Ground Controller
    Added extra details to manual-control.py for easier debugging
    Added target code architecture to relevant files
    Replaced sensitive `int` values with `uint32_t`
    [main.cpp, manual-control.py, motor-control.cpp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]
2026-06-16 Fix serial protocol & motor control
    Rate limited motor updates over serial
    Added PWM protection for motors
    Removed console print from ground controller
    [main.cpp, manual-control.py, motor-control.cpp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]

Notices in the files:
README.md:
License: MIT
